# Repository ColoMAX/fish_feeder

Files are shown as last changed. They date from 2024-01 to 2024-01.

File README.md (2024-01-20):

<h1 align="center">

</h1><br>

# FishFeeder

Standalone automatic fish feeder, based on a ESP8266 with ESPHome.

<p align="center">
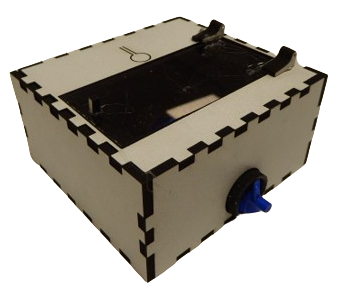
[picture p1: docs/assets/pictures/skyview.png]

</p>

Just dispenses (fish) food using a 3D-printed (archimedean) two flute screw. It uses a modified servo motor to drive the screw, such that it no longer has angle limits. A secondary servo is installed to open a lid of the fish tank, as well as a vibration motor to make the dispenses more consistent. An additional relay can be installed to control some form of lighting.

It is intend to be used stand-alone, but because it is written using the ESPHome project, it can easily be integrated in the rest of your home-automation. The device is configured using a web interface, but can also be controlled manually via the push of a button.

Although the project is build using an ESP8266, other controllers supported by ESPHome (esp32, rp2040, ...) can also be used, with minimal modifications.

## Getting started

Take a look at the [docs](https://ColoMAX.github.io/fishfeeder).

## TODO

- custom css
- Add light control (timer)
- ~~Change order in webserver (create pr esphome feature-request #1774)~~ fixed by prefix numbers

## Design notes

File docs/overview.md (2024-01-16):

# Overview

## Requirements

- [Install ESPHome](https://www.esphome.io) (version 2023.11.6)

## Customization

One can customize this project with ease. A few examples are:

- Instead of ESP8266, use an ESP32 (or variants). For this one would need to substitute `esp8266_pwm` with `ledc` in the yaml file, and change the board.
- Add RGB lighting and heating control by adding a temperature sensor and [Climate controller ESPHome software component](https://esphome.io/components/climate/bang_bang).
- Add graphics to your box by modifying the laser cutter files.
- Add custom lighting effects to mimic a sunrise using [RGB-leds](https://esphome.io/components/light/rgb.html) and the [ESPHome sun component](https://esphome.io/components/sun.html).
- Etc.

### Software

- Add your modifications to the configuration in `src/fishfeeder.yaml`.
  - e.g.: new name, enable home-assistant integration, add other controls, such as RGB lights.
- connect via usb.
- run: `cd src/; esphome run --device /dev/ttyUSB0 fishfeeder.yaml `
- Then connect to wifi access point, or go to the webserver (by default `http://fishfeeder.local:80`) to configure it.

### Mechanical

Do so to your hearts content, all design files are available in the `design/mechanical` directory. Here you can modify the designs if required. The `3mf` files contain the 3D printed parts, the and the rest should be self evident.

There are some software which you might want to install before continuing.

- [PrusaSlicer](https://www.prusa3d.com/page/prusaslicer_424/) to create the gcode for your printer.
- qrencode by running `apt install qrencode`, for a qr code.
- Inkscape by running `apt install inkscape, to modify the laser cutter design.
- LaserWeb or LightBurn, to create the gcode for your cutter.

To generate a QR to this page, which will be put on the box, run `cd design/mechanical; bash qr_make.sh`.

## Build

General idea of electrical connections.

### Parts list

- 1x esp8266 (Wemos D1 mini)
- 2x SG90 micro Servo's
- 3D printer and some (food-safe PLA) filament (approx 7m/21g of filament)
- laser/water cutter with 3mm flat material
- 1x vibration motor (Seeed Studio 316040001)
- 1x stsp momentary switch
- hot glue
- 2x paperclips or metal binding wire (for hinges and lid opening)
- 1x 8x1 pin-header or other connector
- 2x m2 bolts
- 1x acrylic/Plexiglass (approx 39x83mm)

### Assembly

These instructions are not complete, but should give you the general idea, be creative!

- 3D print the screw(`design/mechanical/screw.3mf`) and bucket(`design/mechanical/bucket.3mf`).
- Laser-cut the casing [mechanical/Laser_cut_box.svg](design/mechanical/Laser_cut_box.svg).
- one the servo's needs to be modified for continues rotation. You can follow a few guides online but here is a summary:
      - Remove rotation limit on one of the gears
      - Remove the metal extremities on the base of the potentiometer shaft.
      - De-solder internal potentiometer and add two equivalent resistors, to fool controller in always center position, but keep potentiometer in there, for structural support of gears.
- Solder as described in [electrical/schematic.svg](https://raw.githubusercontent.com/ColoMAX/fishfeeder/master/design/electrical/schematic.svg).
- Use wire and the small pieces from the cutter to create the hinges.
- Screw the continues servo to the bucket.
- Heat the end of the screw in order to press-fit it to the servo.
- Glue to other servo on a 90 degree angle to the previous one.
- Add the headers and hinge and wires between hinge, servo and your aquarium lid.
- Close it all up.

Now continue with [Getting started](getting-started.md).

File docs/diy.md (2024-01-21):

# Making your own

## Customization

One can customize this project with ease. A few examples are:

- Instead of ESP8266, use an ESP32 (or variants), by simply changing the configuration in `fishfeeder.yaml`.
- Add RGB lighting and heating control by adding a temperature sensor and [Climate controller ESPHome software component](https://esphome.io/components/climate/bang_bang).
- Add graphics to your box by modifying the laser cutter files.
- Add custom lighting effects to mimic a sunrise using [RGB-leds](https://esphome.io/components/light/rgb.html) and the [ESPHome sun component](https://esphome.io/components/sun.html).
- Etc.

### Software

### Requirements

- Install [ESPHome](https://www.esphome.io) (version 2023.11.6)

After that you can start to work on the software.

- Add your modifications to the configuration in `src/fishfeeder.yaml`.
  - e.g.: new name, enable home-assistant integration, add other controls, such as RGB lights.

### Flashing firmware

- connect via usb.
- run: `cd src/; esphome run --device /dev/ttyUSB0 fishfeeder.yaml `
- Then connect to wifi access point, or go to the webserver (by default `http://fishfeeder.local:80`) to configure it.

> Alternatively you can use the browser based uploading, with a generic firmware image on [this page](burner.html). And if you which, upload your modifications using OTA uploads after that.

### Mechanical

Do so to your hearts content, all design files are available in the `design/mechanical` directory. Here you can modify the designs if required. The `3mf` files contain the 3D printed parts, the and the rest should be self evident.

There are some software which you might want to install before continuing:

- [PrusaSlicer](https://www.prusa3d.com/page/prusaslicer_424/) to create the gcode for your printer.
- qrencode by running `apt install qrencode`, for a qr code.
- Inkscape by running `apt install inkscape, to modify the laser cutter design.
- LaserWeb or LightBurn, to create the gcode for your cutter.

To generate a QR to this page, which will be put on the box, run `cd design/mechanical; bash qr_make.sh`.

## Build

General idea of electrical connections.

### Parts list

- 1x esp8266 (Wemos D1 mini)
- 2x SG90 micro Servo's
- 3D printer and some (food-safe PLA) filament (approx 7m/21g of filament)
- laser/water cutter with 3mm flat material
- 1x vibration motor (Seeed Studio 316040001)
- 1x stsp momentary switch
- hot glue
- 2x paperclips or metal binding wire (for hinges and lid opening)
- 1x 8x1 pin-header or other connector
- 2x m2 bolts
- 1x acrylic/Plexiglass (approx 39x83mm)

### Assembly

These instructions are not complete, but should give you the general idea, be creative!

- 3D print the screw(`design/mechanical/screw.3mf`), bucket(`design/mechanical/bucket.3mf`) and optionally the cap (via `GNU make` to generate the `.3mf`).
- Laser-cut the casing `design/mechanical/Laser_cut_box.svg`.
- one the servo's needs to be modified for continues rotation. You can follow a few guides online but here is a summary:
      - Remove rotation limit on one of the gears
      - Remove the metal extremities on the base of the potentiometer shaft.
      - De-solder internal potentiometer and add two equivalent resistors, to fool controller in always center position, but keep potentiometer in there, for structural support of gears.
- Solder as described in [electrical/schematic.svg](https://raw.githubusercontent.com/ColoMAX/fishfeeder/master/design/electrical/schematic.svg).
- Use wire and the small pieces from the cutter to create the hinges.
- Screw the continues servo to the bucket.
- Heat the end of the screw in order to press-fit it to the servo.
- Glue to other servo on a 90 degree angle to the previous one.
- Add the headers and hinge and wires between hinge, servo and your aquarium lid.
- Close it all up.

Now continue with [Getting started](getting-started.md).

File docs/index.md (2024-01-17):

# FishFeeder Documentation

Welcome to the official documentation for the FishFeeder project! Whether you're a user looking to set up, maintain the device or a DIY enthusiast eager to build your own, you'll find the information you need here.

## Table of Contents

- [Getting Started](getting-started.md)
      - [Initial Setup](getting-started.md#Initial Setup)
      - [Configuration](getting-started.md#configuration)
      - [Maintenance](getting-started.md#maintenance)
      - [Troubleshooting](getting-started.md#troubleshooting)

- [DIY](diy.md)
      - [Making your own](diy.md#making-your-own)
      - [Requirements](diy.md#requirements)
      - [Customization](diy.md#customization)
      - [Build](diy.md#build)
            - [Parts List](diy.md#parts_list)
            - [Assembly](diy.md#assembly)

## Getting Started

If you are new to the FishFeeder project, start with the user documentation to learn how to set up and use the device. If you are interested in building your own FishFeeder, check out the DIY section for a guide.

## Contribution

Contributions to the documentation are welcome! If you find any issues or have suggestions, feel free to open an [issue](https://github.com/ColoMAX/fishfeeder/issues) or submit a [pull request](https://github.com/ColoMAX/fishfeeder/pulls).

## License

This documentation is licensed under [MIT License](LICENSE) - feel free to use, share, and modify.

Happy fish feeding!

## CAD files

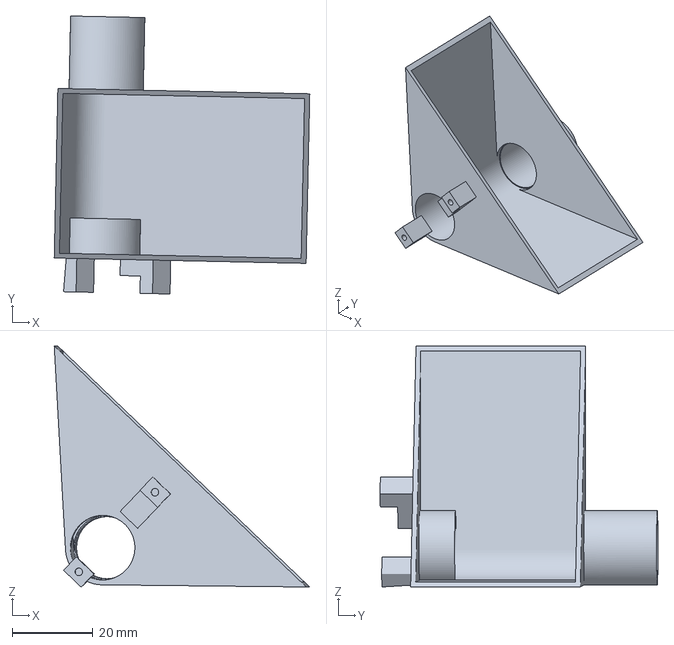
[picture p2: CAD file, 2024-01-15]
design/mechanical/bucket.3mf
63.3 x 68.8 x 59.7 mm

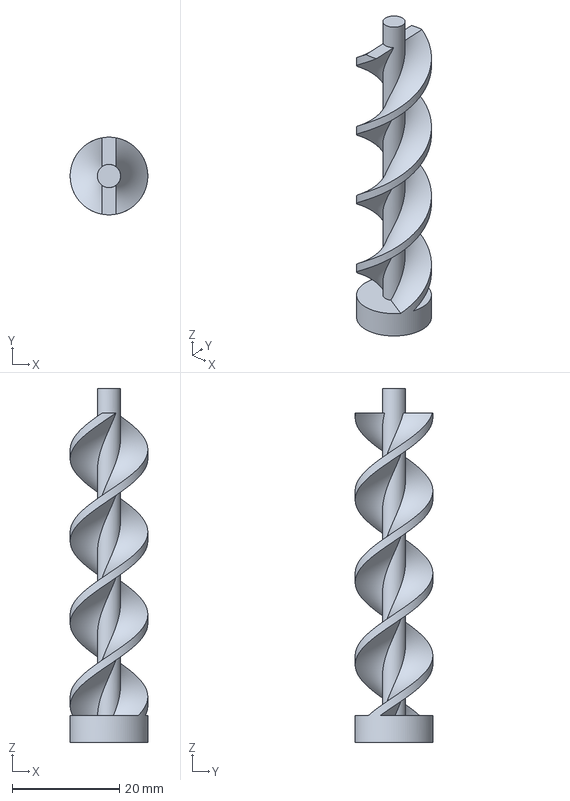
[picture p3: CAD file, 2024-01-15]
design/mechanical/screw.3mf
14.5 x 14.5 x 66.0 mm

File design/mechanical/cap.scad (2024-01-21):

$fa = 0.01;
$fn = 80;
height_tube = 12 + 8;
tube_id = 19.1;
tube_wall_thinkness = 1.6;
dispo_length_extra = 10;
dispo_length = dispo_length_extra + tube_id / 2 + tube_wall_thinkness;
tube_recess = 4.5;

difference()
{
    union()
    {
        cylinder(h = height_tube, d = tube_id + tube_wall_thinkness * 2);
        // translate([-(tube_id+tube_wall_thinkness*2)/2,-tube_wall_thinkness])
        // cube([tube_id+tube_wall_thinkness*2,dispo_length,height_tube ]);
    }
    translate([ 0, 0, -tube_wall_thinkness ]) cylinder(h = height_tube, d = tube_id);
    translate([ -tube_id / 2, 0, tube_recess ]) cube([ tube_id, dispo_length, height_tube - tube_recess ]);
    translate([ -1 / 2, tube_id / 2 - 0.1 / 2, -0.01 / 2 ]) cube([ 1, tube_wall_thinkness + 0.1, tube_recess + 0.01 ]);
}

difference()
{
    union()
    {
        // cylinder(h = height_tube, d = tube_id+tube_wall_thinkness*2);
        translate([ -(tube_id + tube_wall_thinkness * 2) / 2, -tube_wall_thinkness ])
            cube([ tube_id + tube_wall_thinkness * 2, dispo_length, height_tube ]);
    }
    translate([ 0, 0, -tube_wall_thinkness ]) cylinder(h = height_tube, d = tube_id);
    translate([ -tube_id / 2, 0, -tube_wall_thinkness ]) cube([ tube_id, dispo_length, height_tube ]);
}

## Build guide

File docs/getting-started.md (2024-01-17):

# Getting started

If you do not already have the fishfeeder, than first go to [Making your own](diy.md#making-your-own) before continuing this document.

The fishfeeder

## Initial Setup

- Power on the device by connecting the power port (likely a micro-usb or usb-C port on the device). The device should not pull more than 500mA at 5v, thus any usb power source should suffice, but do mind to use a short or high quality usb cable.
  > Tip: you can test whether the device is properly working, by pressing the button on the top for around 1 second. The dispenser screw should start to turn and stop as you release it. If not, there is likely something wrong with your power connection.
- The first time your power on the device, it will create a WiFi access point, named "FishFeeder Hotspot". Connect to it using the password `SomethingFishy`.
- Now your device should ask you, or redirect you towards the configuration page of the device. If not, you can manually go to the website `http://192.168.4.1`, making sure you are still connected to the access point of the fishfeeder.
  > Alternatively you can try to connect the device via usb to your computer and visit [Improv via Serial](https://www.improv-wifi.com/) to set the initial WiFi credentials directly, without using the hotspot. **NOTE** not all browsers support this feature, the site will indicate if so.
- (optional) Here you can apply any updates (`*.bin` e.g. `firmware.bin` file) if provided to you.
- Now you can configure you WiFI settings inside of the fishfeeder.
- After successfully submitting you WiFi credentials to the device, you should see the access point disappear. After which you should be able to connect to the general configuration panel of the device by navigating to `http://fishfeeder.local`.
- In this configuration panel you can modify the feeding schedule and amount.
  > Tip: you can test the amount dispensed per feeding time, by doing a manual feed via this configuration panel. Do make sure you added enough fish food in the top compartment of the device.
- After your are done configuring, you can safely exit the configuration, but do not unplug the device right away. The settings will be store automatically after a few moments (within 1 minute).

## Configuration

- Open the configuration page when connected to the same WiFi network as your fishfeeder.
- Navigate to `http://fishfeeder.local`.
- Now you should be greeted with the configuration page.

The feeder will dispense a configurable amount of food based on a schedule you can provide. This schedule can be configured to be active only on certain days (`Once every ...  days`), such as; each day (1), every second day (2), one a week (7).
Then on those days, you get set a starting and ending time, in which the feeder can dispense. Within this time frame, you can set the number of times it will need to feed.

You can configure the amount dispensed per feeding, which is an *arbitrary scale*, so test it out. This can be done by modifying the scale, and than pressing the manual feed button on the webpage to dispense this amount.

## Maintenance

From the configuration page you can also apply updates manually if you have access to an update file, by uploading the `.bin` file.

You may also visit the [release page](https://github.com/ColoMAX/fishfeeder/releases/) to retrieve generic firmware updates.

## Troubleshooting

- Make sure yo have a **proper power supply** and a working power cable connected to the feeder.
- If you are unable to do a firmware update, you can try to restart in safe-mode, vai the configuration webpage, before uploading the file.
- If you have troubles with applying your new schedule, you may want to reset the scheduler, which you also can do via the webinterface. After which you should be able to see that the last feed time changed.
- If you are helpless you can also try to reset to **factory defaults**:
      - If you can access the configuration webpage, you can reset back to factory defaults over there.
      - If not, you can use the button on the device itself: You need to do three rapid salvos of one short press, then one longer (0.5 seconds), similar to a heartbeat. 10 seconds after the lasst lomg press, will it vibrate (assuming vibration motor is installed), and do the factory reset.
  > Note that his will not revert any firmware updates.

Lastly you can try to submit a new issue on github if you are not able to figure it out yourself.

### Known bugs

- After an update has been performed via ota (WiFi), the running feeding sum can be lost and will display the wrong value. A subsequent factory reset will also not reset the counter to 0.

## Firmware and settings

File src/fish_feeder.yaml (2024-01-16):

esphome:
  name: fishfeeder
  on_boot:
      priority: 800
      then:
        - lambda: |-
            id(last_update_str).publish_state(strtok(ctime(&id(last_timestamp)), "\n"));
            char fsbuf[15];
            snprintf(fsbuf, sizeof(fsbuf), "%.2g", id(feed_sum));
            id(feed_sum_str).publish_state(fsbuf);

preferences:
  flash_write_interval: 1min

esp8266:
  board: d1_mini
  restore_from_flash: true

# Enable logging
logger:

# Enable Home Assistant API
#api:

ota:
  password: SomethingFishy # Add pass

wifi:
  ap:
    ssid: "Fish Feeder Hotspot"
    password: SomethingFishy
captive_portal:

web_server:
  port: 80
  log: false

globals:
  - id: last_timestamp # to keep track of days interval
    type: time_t
    restore_value: true
    initial_value: "0"
  - id: feed_sum # running total sum of dosages
    type: double
    restore_value: true
    initial_value: "0"
  - id: motor_start_time
    type: struct timeval
    restore_value: false
    initial_value: "{0}"
light:
  - platform: binary
    name: Fish tank light
    output: light_relay

select:
  - platform: template
    name: "First feeding of day"
    restore_value: true
    optimistic: true
    options:
      - "06:00"
      - "06:15"
      - "06:30"
      - "06:45"
      - "07:00"
      - "07:15"
      - "07:30"
      - "07:45"
      - "08:00"
      - "08:15"
      - "08:30"
      - "08:45"
      - "09:00"
      - "10:00"
      - "11:00"
      - "12:00"
      - "13:00"
      - "14:00"
      - "15:00"
      - "16:00"
      - "17:00"
      - "18:00"
      - "19:00"
      - "20:00"
      - "20:30"
      - "21:00"
      - "21:30"
      - "22:00"
      # - "22:30"
    initial_option: "20:00"
    id: feed_first_time
    icon: mdi:icon7-time
  - platform: template
    name: "Last feeding of day"
    restore_value: true
    optimistic: true
    options:
      # - "06:00"
      - "06:15"
      - "06:30"
      - "06:45"
      - "07:00"
      - "07:15"
      - "07:30"
      - "07:45"
      - "08:00"
      - "08:15"
      - "08:30"
      - "08:45"
      - "09:00"
      - "10:00"
      - "11:00"
      - "12:00"
      - "13:00"
      - "14:00"
      - "15:00"
      - "16:00"
      - "17:00"
      - "18:00"
      - "19:00"
      - "20:00"
      - "20:30"
      - "21:00"
      - "21:30"
      - "22:00"
      - "22:30"
    initial_option: "21:00"
    id: feed_last_time
    icon: mdi:icon7-time
number:
  - platform: template
    name: Number times per day
    min_value: 1
    max_value: 10
    step: 1
    initial_value: 1
    restore_value: true
    id: feed_num_per_day
    optimistic: true
    icon: mdi:icon7-th-list
  - platform: template
    name: Once every ...  days
    min_value: 1
    max_value: 14
    step: 1
    initial_value: 1
    restore_value: true
    id: feed_day_interval
    optimistic: true
    icon: mdi:icon7-table
    set_action:
      then: # not nessasary, but otherwise function might be weird fo rthe user, since living things likely will not benefit from such a schedule
        - lambda: |-
            if(x>1) {id(feed_num_per_day).publish_state(1);id(feed_num_per_day).update();}
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

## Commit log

2024-01-15 Fix bug if device has long not been turned on
2024-01-15 Added improv, various reset buttons, info on last feed moment. Made schedule O(1). Added troubleshooting info.
2024-01-17 Change order in webserver interface Added esp32 patch
2024-01-17 Fix UI fault than end can be before start time. Fix link in lasercutter svg. Add strengtheners in casing. Removed on_boot, rather let the other components update (also on sntp sync).
2024-01-20 Added cap. Motor up to 20%, due to lack of torque.
    [cap.scad]
2024-01-21 Shorter cap. Added experimental upload firmware page on docs Removed FF_EPOCH, to trigger on first boot
    [cap.scad]
